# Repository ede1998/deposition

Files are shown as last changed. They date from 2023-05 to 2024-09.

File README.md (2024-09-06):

# Deposition

This repository contains **Deposition** (short for *Desk Position*), a small embedded application that controls the position of an height-adjustable desk.
This is the application in action:

<video src="https://github.com/user-attachments/assets/10c666cf-5465-435d-b400-dcfeb9302840"></video>

[Video of height-adjustable desk moving up and down](./resources/demo.mp4)

## How it works

The micro controller gets inputs via 4 buttons: up, down, position 1, position 2. When one of the buttons is pressed, the desk starts moving.
Required hardware:

- 1x precision potentiometer *Bourns 3590*, supports 10 full rotations
- 1x retractable lanyard/key chain
- 1x OLED 128x64 dot matrix *SSD1306*
- 2x photo coupler *EL817*
- 4x button
- resistors
- cables
- enclosures, 3D printed
- micro controller dev board *ESP32-WROOM-32*

### Position Detection

<video src="https://github.com/user-attachments/assets/6ebd7623-417b-41c7-af76-c692e692968f"></video>

[Video of thread begin pulled, hooked onto screws and released, display shows current distance](./resources/test-bench.mp4)

The current height is detected with the micro controller's builtin ADC which is connected to a potentiometer. This potentiometer is in turn mechanically connected
to the insides of a retractable lanyard with a few 3D printed connectors. The thread of the lanyard is connected to a horizontal stabilizer bar underneath the desk.
When the height increases, the thread is pulled further out and when it is reduced, the spiral torsion (=clock) spring of the lanyard retracts the thread. This in
turn rotates the potentiometer clockwise or counterclockwise. This is how it looks inside:

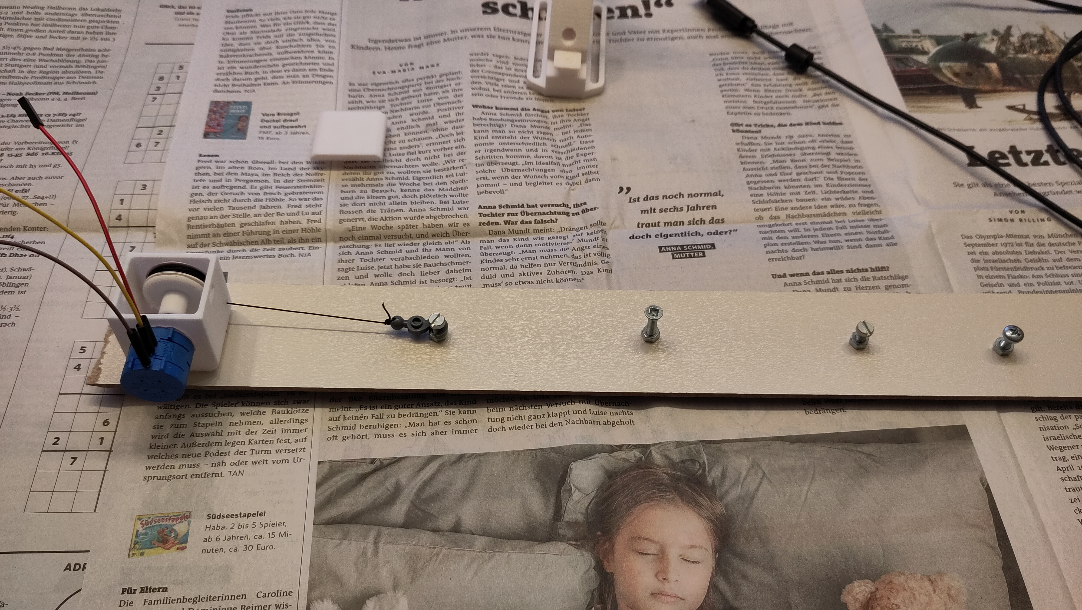
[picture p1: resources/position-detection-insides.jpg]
Insides of a retractable lanyard connected to a potentiometer with a 3D printed part, everything mounted on a long wooden board with screws in regular intervals, a thread is connecting the retractable lanyard to one of the screws


Further details can be found in [resources/height-adjustable-desk.pdf](resources/height-adjustable-desk.pdf).

### Control of the desk motors

The desk is moved by motors located in the desk's legs. The were pre-installed in the commercial product and could be controlled with two buttons: up and down.
However, the control panel did not support moving to a memorized position. For **Deposition**, the buttons were replaced with photo couplers to emulate their
open/closed behavior while keeping the two circuits electrically separated.

The circuit diagram can be found in [resources/height-adjustable-desk.pdf](resources/height-adjustable-desk.pdf).

### Enclosure

The enclosures were designed in FreeCAD and later on in OpenSCAD. They are all 3D printed. All models can be found under <./cad>.

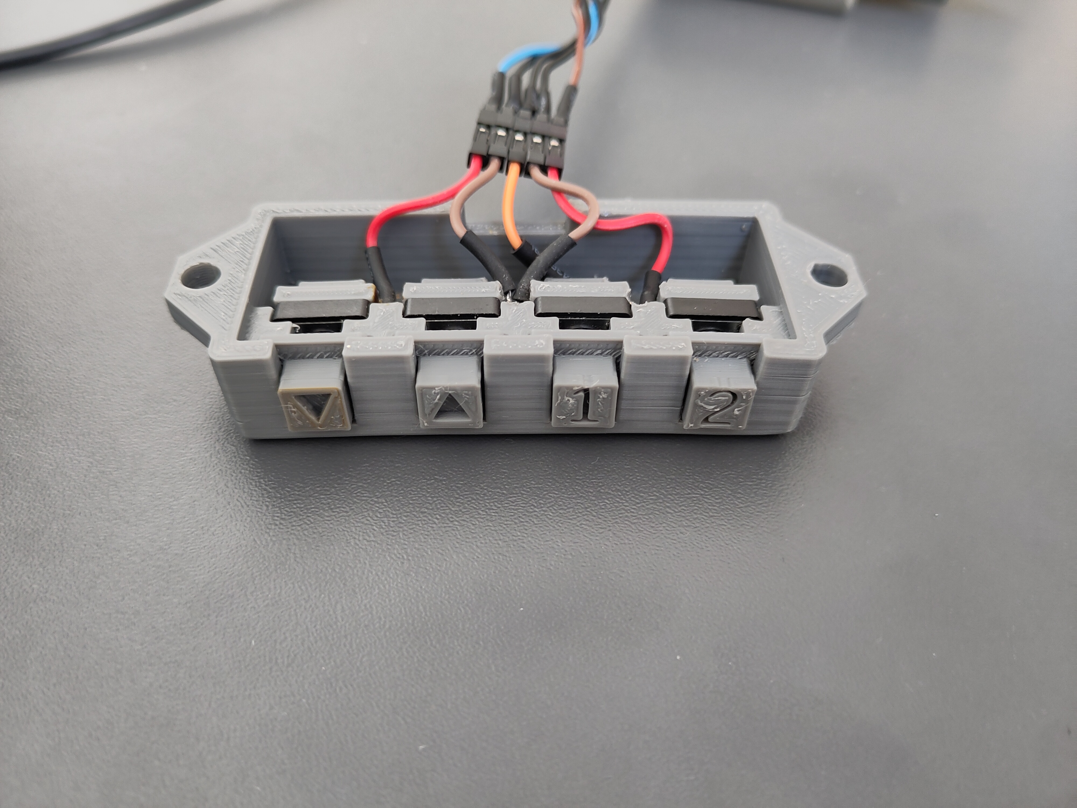
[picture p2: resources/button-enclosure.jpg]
Cuboid enclosure with four button protruding out the front and some cables going out the back


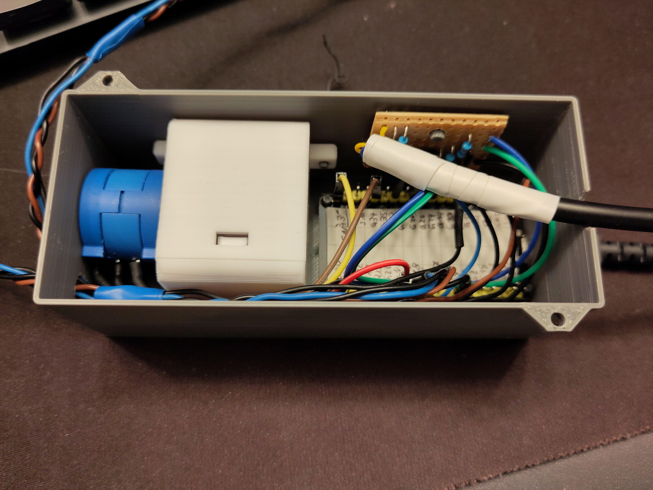
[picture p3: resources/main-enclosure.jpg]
Cuboid enclosure containing ESP32 dev board, potentiometer, a small PCB and lots of cables


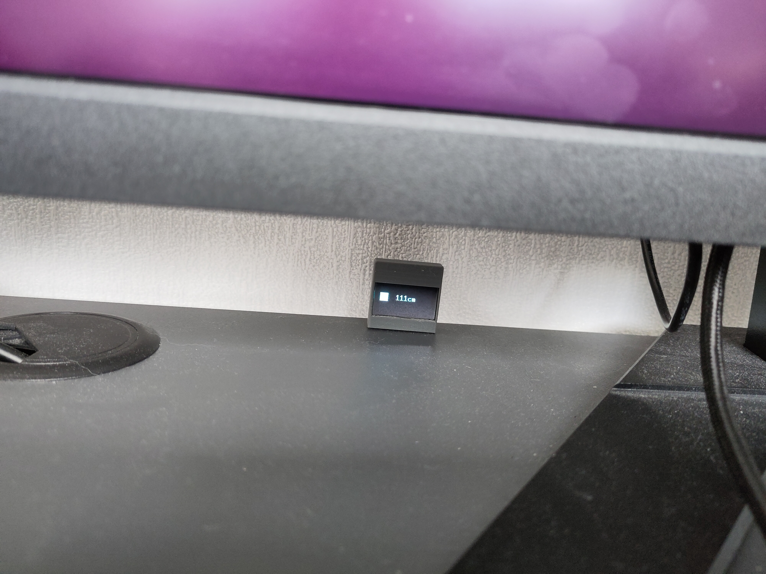
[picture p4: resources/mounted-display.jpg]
Small display inside 3D printed enclosure mounted on rear edge of desk


## Lessons learned

- General 3D design with FreeCAD and OpenSCAD was not hard after getting used to the general design process.
- Rust embedded ecosystem is nice: GPIO pins cannot be used multiple times by accident because you take ownership.
- Twisting wires is a bad idea if they are not a differential pair. I could not even get buttons or display (with 10Hz I2C) to work this way.

## Development environment

In addition to normal Rust, [install the ESP32 Rust toolchain](https://docs.esp-rs.org/book/installation/riscv-and-xtensa.html) via `espup`.
Remember to always `source ~/export-esp.sh`. You can then use the normal `cargo` commands, e.g. `cargo run --release`[^1] to compile and flash
the program onto the micro controller if it is connected.

[^1]: Debug mode will likely not working due to timing-sensitive peripherals.

For testing, [Wokwi](https://github.com/wokwi/wokwi-cli) is available. Unfortunately, the committed test does not work because it fails to read from
the persistent memory. The test can be run with `wokwi-cli --scenario wokwi-tests/go_to_options.test.yaml` if Wokwi is installed in v0.14.0 (and possibly others).
Wokwi also requires the environment variables `WOKWI_CLI_TOKEN` and `GITHUB_TOKEN` to be set.

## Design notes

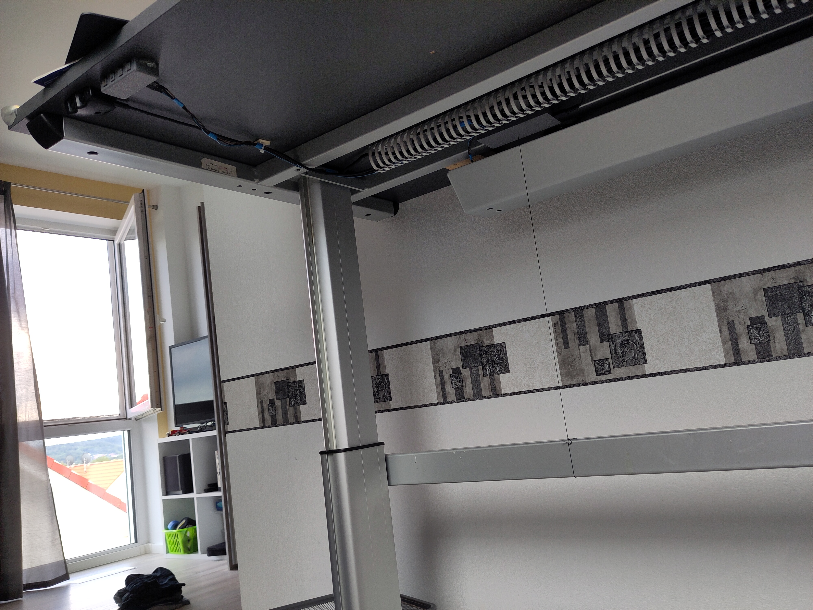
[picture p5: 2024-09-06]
resources/thread-underneath-desk.jpg

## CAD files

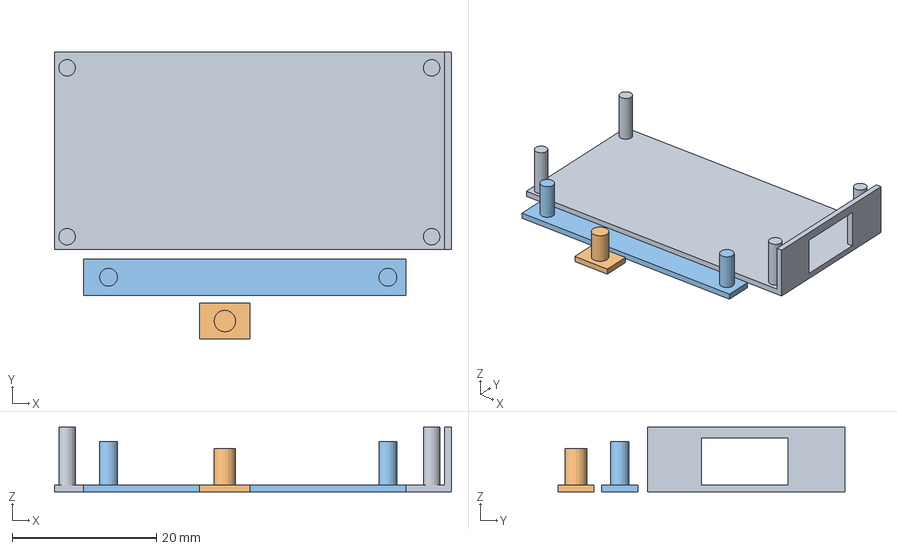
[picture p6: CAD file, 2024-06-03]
cad/SS_main-housing_test.3mf
55.0 x 39.8 x 9.00 mm
main-housing_esp_test.stl(2)
main-housing_opto_test.stl
main-housing_spool_test.stl

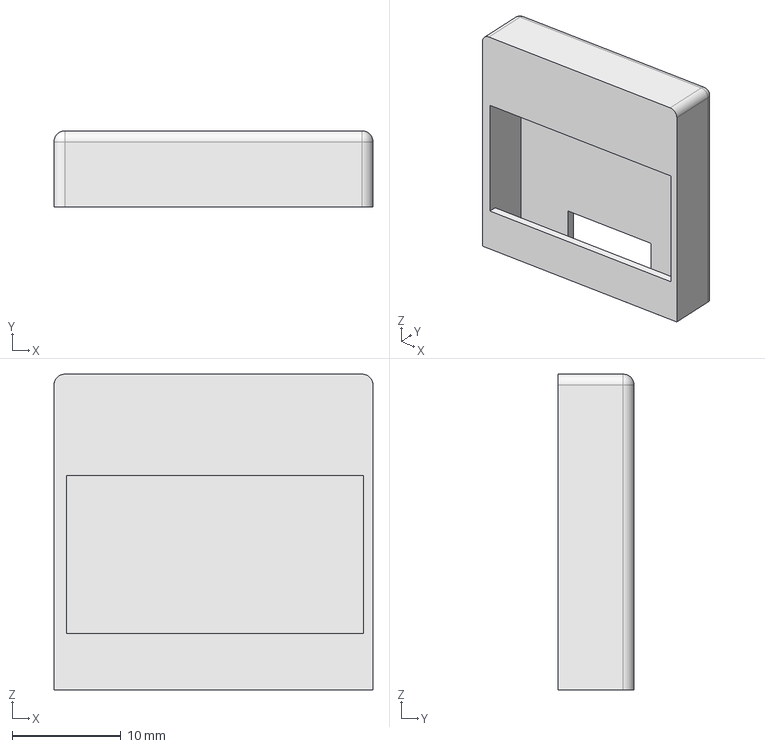
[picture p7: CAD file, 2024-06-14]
cad/display-housing.FCStd
29.3 x 7.00 x 29.0 mm

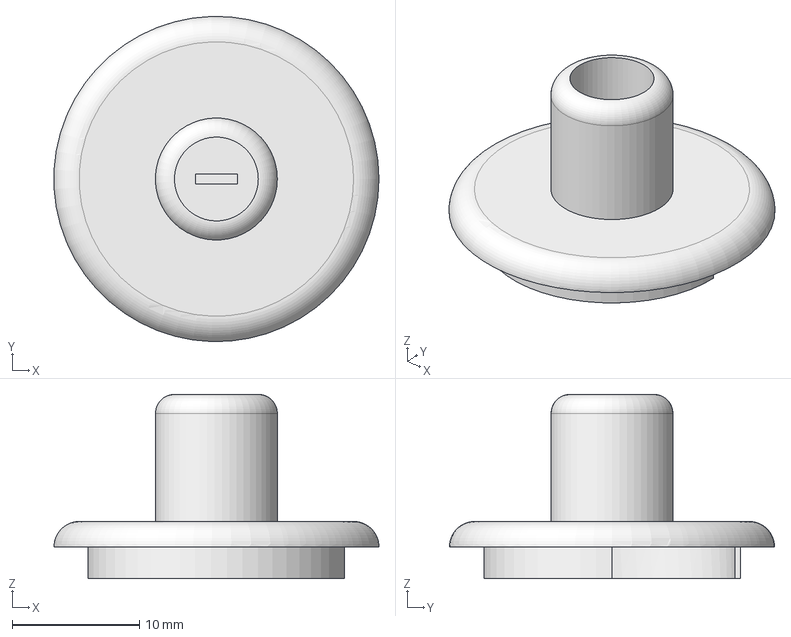
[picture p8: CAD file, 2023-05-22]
cad/poti-connector.FCStd
25.6 x 25.6 x 14.5 mm

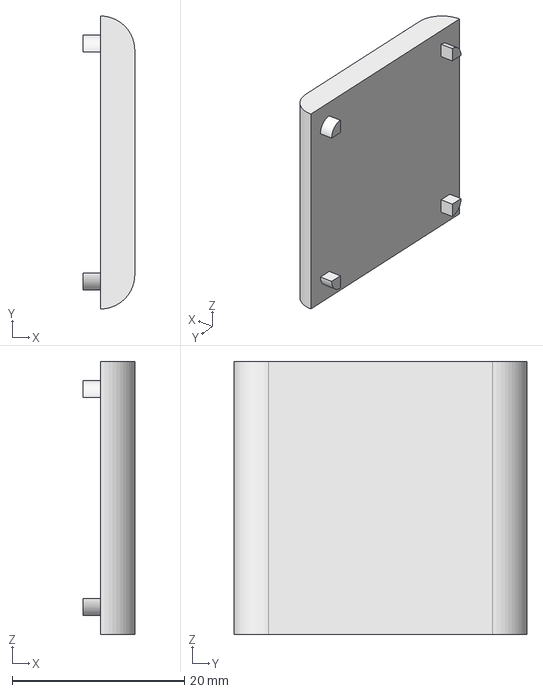
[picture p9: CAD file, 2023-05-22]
cad/minimal-case.FCStd
6.00 x 34.0 x 31.7 mm

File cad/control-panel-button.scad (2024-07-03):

include <BOSL/constants.scad>
use <BOSL/transforms.scad>
use <BOSL/shapes.scad>

$fn = 20;

touch_area = [7.5, 7.5, 5];
engraving_depth = 1.6;
retainer = [13,13,1.5];
engraving =
    //"1";
    //"2";
    //"▲";
    "▼";

upcube(retainer);
up(retainer.z) {
    difference() {
        upcube(touch_area);
        up(touch_area.z) mirror([0,0,1]) linear_extrude(engraving_depth) text(engraving, size = 6.5, valign = "center", halign = "center");
    }
}

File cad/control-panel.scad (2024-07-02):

include <BOSL/constants.scad>
use <BOSL/masks.scad>
use <BOSL/shapes.scad>

$fn = 20;

container_inner = [65, 25, 12.3];
container_thickness = 3;

connector_gap_height = 3.5;
connector_gap_width = 13.7;

button_height = 11.9;
button_length = 11.9;
button_base_width = 3.7;
button_prongs_distance = 12.5;
button_prongs_length = 2.8;
button_clicker_bump = 3.3;
button_clicker_clearance = 0.3;

button_face = 8;

module brace(lengths, height, thicknesses) {
    assert(len(lengths) == 2, "Requires 2 length values, one for each leg");
    assert(len(thicknesses) == 2, "Requires 2 thickness values, one for each leg");
    linear_extrude(height = height)
        polygon(points = [[0,0], [0, thicknesses.y], [lengths.x, thicknesses.y], [lengths.x, thicknesses.y + lengths.y], [lengths.x + thicknesses.x, thicknesses.y + lengths.y], [lengths.x + thicknesses.x,0]]);
}


module button_brace() {
    brace_thickness = 3;
    button_center_x = button_length / 2 + brace_thickness;
    cover_brace_thickness = [2,2];
    cover_brace_lengths = [3,2.4];
    cover_length = button_length +2;
    cover_brace_start_y = - (button_clicker_bump - brace_thickness);
    
    translate([-button_center_x, cover_brace_lengths.y  - brace_thickness + (button_clicker_bump - button_clicker_clearance), 0]) {
        translate([button_center_x - 0.5 * button_prongs_distance, button_base_width + brace_thickness,0]) cube([button_prongs_distance, button_prongs_length, button_height]);
        extra_support = [button_prongs_distance * 0.7, 4, button_height * 0.8];
        translate([button_center_x - 0.5 * extra_support.x, button_base_width + brace_thickness + button_prongs_length, 0]) cube(extra_support);
        
        translate([2*brace_thickness,0,0]) mirror([1,0,0]) brace([brace_thickness, brace_thickness], button_height, [brace_thickness, brace_thickness - 0.2]);
        translate([button_length,0,0]) brace([brace_thickness, brace_thickness], button_height, [brace_thickness, brace_thickness - 0.2]);
    }
    
    translate([-button_center_x, cover_brace_lengths.y + cover_brace_thickness.y - cover_brace_start_y, 0]) {
        distance_from_center = 0.5 * cover_length - cover_brace_lengths[0];
        translate([button_center_x + distance_from_center, cover_brace_start_y,0]) mirror([0,1,0]) brace(cover_brace_lengths, button_height, cover_brace_thickness);
        translate([button_center_x - distance_from_center, cover_brace_start_y,0]) rotate([0,0,180]) brace(cover_brace_lengths, button_height, cover_brace_thickness);
    }
}

module screw_fixture(diameter, thickness) {
    side = diameter * 1.5;
    translate([-2*side, -side, 0]) difference() {
        cube([side, side, thickness]);
        translate([side/2,side/2, -thickness*0.05]) cylinder(h = thickness * 1.1, d = diameter);
    }
    translate([-side,0,0]) rotate([90,0,0]) right_triangle([side, thickness, side]);
    translate([-2*side,0,0]) rotate([90,0,-90]) right_triangle([side, thickness, side]);
}

module main() {
    translate([0,0, 0.5 * container_inner.z]) difference() {
        cuboid([container_inner.x + container_thickness * 2, container_inner.y + container_thickness * 2, container_inner.z + container_thickness], fillet=2, edges = EDGES_ALL - EDGES_TOP);
        cube(container_inner, center = true);
        translate([0,0, 0.8*container_inner.z]) cube(container_inner, center = true); // Remove roof
        for (i = [-1.5:1.5]) {
            translate([i * (button_length + 4), -0.5*container_inner.y, (button_length + 5)/2-0.5*container_inner.z]) cube([button_face,container_thickness*2.5, button_face+5], center = true);
        }
        translate([0, container_inner.y / 2 - 0.5 * container_thickness, container_inner.z / 2 + container_thickness - connector_gap_height + 0.25])
            backcube([connector_gap_width, container_thickness * 2, connector_gap_height]);
    }
    
    button_start_y = -container_inner[1] /2;
    for (i = [-1.5:1.5]) {
        translate([i * (button_length + 4), button_start_y, 0]) button_brace();
    }
    
    diameter = 5;
    thickness = 4;
    screw_fixture_position_xy = [container_inner.x / 2 + container_thickness, 4.5 * 0.5 * diameter];
    screw_fixture_position_z = container_inner.z - thickness + container_thickness / 2;
    translate(concat(screw_fixture_position_xy, screw_fixture_position_z))
        rotate([0,0,90])
            screw_fixture(diameter = diameter, thickness = thickness);
    translate(concat(-1 *screw_fixture_position_xy, screw_fixture_position_z))
        rotate([0,0,270])
            screw_fixture(diameter = diameter, thickness = thickness);
}

intersection() {
    main();
//    translate([5.5,-7,-2]) cube([button_length+8,24,button_height+container_thickness + 30], center = true);
//    #translate([3.5,width/2+3,-5.5]) rotate([0,0,180]) cube([spool_fixture_distance + 6, wall_thickness * 5, 5]); // spool
//    #translate([23.5,width/2-15,8.5]) cube([7, wall_thickness * 10, 5]); // optocoupler
}

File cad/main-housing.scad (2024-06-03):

include <BOSL/constants.scad>
use <BOSL/masks.scad>
use <BOSL/shapes.scad>

$fn = 20;
wall_thickness = 2;
length = 110;
width = 45;
height = 40;

esp_mount_hole_diameter = 2.3;
esp_mount_hole_distance_long = 50.7;
esp_mount_hole_distance_short = 23.4;
esp_mount_hole_distance_front = 1.5;

spool_fixture_distance = 38.7;
spool_fixture_diameter = 2.2;
yarn_hole_radius = 1;
yarn_hole_distance_from_bottom = 10;
yarn_hole_distance_from_closer_fixture = 8.4;

usb_hole_width = 9.3;
usb_hole_height = 4;

module spool() {
    rotate([-90,0,-90]) {
        import("minimal-case-body_lid.stl");
        import("minimal-case-body_body.stl");
        translate([0,0,-19.8]) cylinder(h = 19.8, d = 22.3);
    }
}
module esp() {
    cube([54.6, 28.3, 13.0], center = true);
}

module optocouplers() {
    cube([31, 8, 24], center = true);
}

%translate([27,0,-10]) union() {
    esp();
    translate([-61,0,7]) spool();
    translate([0, width/2 - 4, 15]) optocouplers();
}

module spool_fixtures(height) {
    rotate([90, 0, 0]) union() {
        cylinder(h = height, d = spool_fixture_diameter);
        translate([-spool_fixture_distance, 0, 0]) cylinder(h = height, d = spool_fixture_diameter);
    }
}

module yarn_hole() {
    hull_bottom = -(height + wall_thickness) / 2;
    pos_short = width/2 - yarn_hole_distance_from_bottom;
    pos_long = -yarn_hole_distance_from_closer_fixture+spool_fixture_diameter/2;
    translate([pos_long, pos_short, hull_bottom - wall_thickness * 0.5])
        cylinder(h = wall_thickness * 1.5, r = yarn_hole_radius);
}

module usb_hole() {
    translate([length/2,0,-(height-usb_hole_height)/2])
        cube([wall_thickness*1.5, usb_hole_width, usb_hole_height], center = true);
}

module esp_mount_fixtures(fixture_height) {
    translate([wall_thickness + esp_mount_hole_distance_front - esp_mount_hole_diameter/2 + 0.2, -esp_mount_hole_distance_short / 2, -height/2])
        union() {
            cylinder(h = fixture_height, d = esp_mount_hole_diameter);
            translate([esp_mount_hole_distance_long,0,0]) cylinder(h = fixture_height, d = esp_mount_hole_diameter);
            translate([0,esp_mount_hole_distance_short,0]) cylinder(h = fixture_height, d = esp_mount_hole_diameter);
            translate([esp_mount_hole_distance_long,esp_mount_hole_distance_short,0]) cylinder(h = fixture_height, d = esp_mount_hole_diameter);
        }
}

module optocouplers_fixture(fixture_height) {
    rotate([90,0,0]) cylinder(h = fixture_height, d = 3.3);
}

module cables_hole(diameter) {
    rotate([0,90,0]) translate([0,0,-wall_thickness]) cylinder(h = wall_thickness * 1.5, d = diameter);
}

module screw_fixture(diameter, thickness) {
    side = diameter * 1.5;
    translate([-2*side, -side, 0]) difference() {
        cube([side, side, thickness]);
        translate([side/2,side/2, -thickness*0.05]) cylinder(h = thickness * 1.1, d = diameter);
    }
    translate([-side,0,0]) rotate([90,0,0]) right_triangle([side, thickness, side]);
    translate([-2*side,0,0]) rotate([90,0,-90]) right_triangle([side, thickness, side]);
}

module main() {
    // basic hull
    let (
        container_inner = [length, width, height],
        container_outer = [ for (i = container_inner) i + wall_thickness ]
    ) {
        difference() {
            fillet(fillet=1.5, size=container_outer, edges=EDGES_Z_ALL, $fn=24) {
                cube(container_outer, center = true); // outer wall
            }
            cube(container_inner, center = true); // inner empty space
            translate([0, 0, height / 2]) cube([length, width, height], center = true); // remove top
            yarn_hole();
            usb_hole();
            translate([-length/2,-0.7 * width/2,0]) cables_hole(diameter = 5);
        }
    }
    
    translate([1, width/2, -3]) spool_fixtures(height = 6);
    esp_mount_fixtures(fixture_height = 8);
    translate([27, width/2, 11]) optocouplers_fixture(fixture_height = 5);
    
    screw_fixture_position_xy = [length / 2 - wall_thickness, - 0.5 * (width + wall_thickness)];
    screw_fixture_position_z = height / 2 - 2;
    translate(concat(screw_fixture_position_xy, screw_fixture_position_z)) screw_fixture(diameter = 3, thickness = 3);
    translate(concat(-1 *screw_fixture_position_xy, screw_fixture_position_z))
        rotate([0,0,180])
            screw_fixture(diameter = 3, thickness = 3);
}

intersection() {
    main();
//    #translate([1,-width/2+9,-height/2-wall_thickness]) cube([esp_mount_hole_distance_long + 6,esp_mount_hole_distance_short + 4,wall_thickness * 5]); // esp
//    #translate([3.5,width/2+3,-5.5]) rotate([0,0,180]) cube([spool_fixture_distance + 6, wall_thickness * 5, 5]); // spool
//    #translate([23.5,width/2-15,8.5]) cube([7, wall_thickness * 10, 5]); // optocoupler
}

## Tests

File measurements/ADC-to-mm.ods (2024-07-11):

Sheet: Sheet1
ADC | mm
952 | 86
1432 | 172
1893 | 258
2204 | 316
2572 | 386
 | 952 | 86
 | 2572 | 386
slope | 0,185185185185185 | 94,8148148148148
offset | -90,2962962962963 | -46231,7037037037
1000 | 94,8888888888889
1200 | 131,925925925926
1400 | 168,962962962963
1600 | 206
1800 | 243,037037037037
2000 | 280,074074074074
2200 | 317,111111111111
2400 | 354,148148148148
2600 | 391,185185185185

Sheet: Sheet2
No-capa | With-capa
2570 | 2598
2543 | 2603
2572 | 2603
2543 | 2600
2571 | 2609
2568 | 2601
2569 | 2604
2575 | 2599
2560 | 2602
2575 | 2607
2580 | 2605
2575 | 2602
2560 | 2601
2550 | 2604
2574 | 2595
2548 | 2607
2580 | 2590
2572 | 2606
2564 | 2597
2573 | 2597
2570 | 2598
2546 | 2604
2576 | 2607
2575 | 2598
2575 | 2607
2562 | 2603
2569 | 2600
2569 | 2607
2573 | 2604
2544 | 2602
2563 | 2605
2561 | 2607
2560 | 2595
2542 | 2605
2585 | 2607
2560 | 2613
2570 | 2598
2574 | 2607
2579 | 2589
2550 | 2603
2575 | 2607
2570 | 2605
2572 | 2602
2565 | 2600
2561 | 2598
2571 | 2590
2560 | 2596
2569 | 2604
2573 | 2604
2543 | 2605
2561 | 2606
2560 | 2600
2578 | 2609
2575 | 2596
2569 | 2606
2561 | 2605
2572 | 2598
2550 | 2609
2573 | 2598
2565 | 2607
2575 | 2594
2575 | 2605
2569 | 2607
2560 | 2606
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

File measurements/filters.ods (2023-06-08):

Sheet: mov_avg_3
2577 | 2569
2506 | 2541
2589 | 2557
2589 | 2561
2495 | 2557
2565 | 2549
2447 | 2502
2576 | 2529
2591 | 2538
2607 | 2591
2604 | 2600
2494 | 2568
2600 | 2566
2589 | 2561
2594 | 2594
2602 | 2595
2548 | 2581
2596 | 2582
2507 | 2550
2590 | 2564
2524 | 2540
2524 | 2546
2576 | 2541
2573 | 2557
2584 | 2577
2587 | 2581
2584 | 2585
2576 | 2582
2586 | 2582
2565 | 2575
2585 | 2578
2606 | 2585
2607 | 2599
2501 | 2571
2450 | 2519
2607 | 2519
2462 | 2506
2584 | 2551
2602 | 2549
2593 | 2593
2469 | 2554
2561 | 2541
2526 | 2518
2448 | 2511
2582 | 2518
2575 | 2535
2584 | 2580
2586 | 2581
2590 | 2586
2582 | 2586
2581 | 2584
2580 | 2581
2592 | 2584
2460 | 2544
2498 | 2516
2584 | 2514
2589 | 2557
2477 | 2550
2475 | 2513
2467 | 2473
2584 | 2508
2587 | 2546
2581 | 2584
2473 | 2547
2579 | 2544
2575 | 2542
2575 | 2576
2584 | 2578
2459 | 2539
2515 | 2519
2488 | 2487
2575 | 2526
2589 | 2550
2456 | 2540
2607 | 2550
2444 | 2502
2478 | 2509
2496 | 2472
2588 | 2520
2592 | 2558
2590 | 2590
2506 | 2562
2544 | 2546
2481 | 2510
2497 | 2507
2574 | 2517
2517 | 2529
2591 | 2560
2457 | 2521
2490 | 2512
2606 | 2517
2592 | 2562
2591 | 2596
2560 | 2581
2575 | 2575
2495 | 2543
2604 | 2558
2589 | 2562
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

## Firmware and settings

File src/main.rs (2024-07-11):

#![no_std]
#![no_main]
#![feature(type_alias_impl_trait)]

use debouncr::DebouncerStateful;
use embassy_time::{Duration, Instant, Ticker, Timer};
use embedded_graphics::{draw_target::DrawTarget, pixelcolor::BinaryColor};
use esp_backtrace as _;
use esp_println::logger::init_logger;
use hal::{
    analog::adc::{Adc, AdcConfig, AdcPin, Attenuation},
    clock::ClockControl,
    gpio::{Gpio34, Io, Level, Pull},
    i2c::I2C,
    peripherals::{Peripherals, ADC1},
    prelude::*,
    system::SystemControl,
    timer::timg::TimerGroup,
};
use heapless::String;
use ssd1306::{prelude::*, I2CDisplayInterface, Ssd1306};

mod data;
mod gui;
mod input;
mod operation_mode;
mod storage;
mod string_format;

use crate::{
    data::{Direction, CALIBRATION, DIRECTION, GUI_MENU, HEIGHT, INPUT, RAW_HEIGHT},
    input::{Inputs, State},
    storage::CONFIGURATION,
};

async fn poll<T, E>(mut f: impl FnMut() -> nb::Result<T, E>) -> Result<T, E> {
    loop {
        match f() {
            Ok(ok) => break Ok(ok),
            Err(nb::Error::Other(err)) => break Err(err),
            Err(nb::Error::WouldBlock) => {} // todo: do we want to keep a busy loop here? the measure task starved with this: `embassy_futures::yield_now().await,`
        }
    }
}

fn compute_median(samples: &mut [u16]) -> u16 {
    samples.sort_unstable();
    let len = samples.len();
    if len % 2 == 0 {
        let right_mid = samples[len / 2];
        let left_mid = samples[(len / 2) - 1];
        (right_mid + left_mid) / 2
    } else {
        samples[len / 2]
    }
}

const SAMPLE_COUNT: usize = if cfg!(debug_assertions) { 32 } else { 64 };

type InputPin = hal::gpio::AnyInput<'static>;
type OutputPin = hal::gpio::AnyOutput<'static>;

#[embassy_executor::task]
async fn drive(mut up: OutputPin, mut down: OutputPin) {
    up.set_low();
    down.set_low();
    loop {
        Timer::after(Duration::from_millis(5)).await;
        let Some(direction) = DIRECTION.planned().await else {
            continue;
        };
        log::info!("starting to drive in direction {direction}");
        match direction {
            Direction::Up => {
                down.set_low();
                up.set_high();
            }
            Direction::Down => {
                up.set_low();
                down.set_high();
            }
            Direction::Stopped => {
                up.set_low();
                down.set_low();
            }
            Direction::ResetDrive => {
                up.set_high();
                down.set_high();
            }
        }
        DIRECTION.acknowledge(direction).await;
    }
}

#[embassy_executor::task]
async fn read_input(up: InputPin, down: InputPin, pos1: InputPin, pos2: InputPin) {
    struct DebouncedPin {
        pin: InputPin,
        debouncer: DebouncerStateful<u8, debouncr::Repeat2>,
    }

    impl DebouncedPin {
        fn new(pin: InputPin) -> Self {
            let debouncer = debouncr::debounce_stateful_2(false);
            Self { pin, debouncer }
        }

        fn update_input(&mut self, input: &mut State) {
            let active = self.pin.is_low();
            let Some(state) = self.debouncer.update(active) else {
                return;
            };
            match state {
                debouncr::Edge::Rising => input.press(),
                debouncr::Edge::Falling => input.release(),
            }
        }
    }

    let mut up = DebouncedPin::new(up);
    let mut down = DebouncedPin::new(down);
    let mut pos1 = DebouncedPin::new(pos1);
    let mut pos2 = DebouncedPin::new(pos2);

    let mut inputs = Inputs::default();

    loop {
        up.update_input(&mut inputs.up);
        down.update_input(&mut inputs.down);
        pos1.update_input(&mut inputs.pos1);
        pos2.update_input(&mut inputs.pos2);

        *INPUT.lock().await = inputs.clone();

        Timer::after(Duration::from_millis(5)).await;
    }
}

#[embassy_executor::task]
async fn measure_task(gpio34: Gpio34, adc: ADC1) {
    measure(gpio34, adc).await.expect("measure task failed");
}

async fn measure(pin: Gpio34, adc: ADC1) -> Result<(), &'static str> {
    let mut adc1_config = AdcConfig::new();
    let mut pin34 = adc1_config.enable_pin(pin, Attenuation::Attenuation11dB);
    let mut adc1 = Adc::<ADC1>::new(adc, adc1_config);

    let mut calibration = CONFIGURATION.lock().await.get().calibration.clone();

    let mut last_log = Instant::now();
    loop {
        if CALIBRATION.signaled() {
            calibration = CALIBRATION.wait().await;
        }

        let pin25_value = read_sample(&mut adc1, &mut pin34).await?;

        let value = calibration.transform(pin25_value);

        if log::log_enabled!(log::Level::Trace) && last_log.elapsed() > Duration::from_millis(250) {
            log::trace!("new height {} (={pin25_value}) measured", value.as_mm());
            last_log = Instant::now();
        }
        *HEIGHT.lock().await = value;
        RAW_HEIGHT.signal(pin25_value);
        Ticker::every(Duration::from_millis(5)).next().await;
    }
}

async fn read_sample<'a>(
    adc1: &mut Adc<'a, ADC1>,
    pin34: &mut AdcPin<Gpio34, ADC1>,
) -> Result<u16, &'static str> {
    let mut samples = heapless::Vec::<_, SAMPLE_COUNT>::new();
    for _ in 0..samples.capacity() {
        let sample = poll(|| adc1.read_oneshot(pin34))
            .await
            .map_err(|_| "failed to read ADC value")?;

        samples.push(sample).map_err(|_| "failed to store sample")?;
    }

    Ok(compute_median(&mut samples))
}

#[embassy_executor::task]
async fn display_task(i2c: I2C<'static, hal::peripherals::I2C0, hal::Blocking>) {
    display(i2c).await.expect("display task failed");
}

fn str_to_owned<const N: usize>(text: &str) -> String<N> {
    text.try_into()
        .expect("Length of str exceeds String capacity")
}

async fn display(
    i2c: I2C<'static, hal::peripherals::I2C0, hal::Blocking>,
) -> Result<(), String<150>> {
    let interface = I2CDisplayInterface::new(i2c);
    let mut display = Ssd1306::new(interface, DisplaySize128x64, DisplayRotation::Rotate180)
        .into_buffered_graphics_mode();
    display
        .init()
        .map_err(|e| format!(150, "display initialization failed: {e:?}"))?;

    loop {
        let menu = GUI_MENU.wait().await;

        display
            .clear(BinaryColor::Off)
            .map_err(|e| format!(150, "clearing display failed: {e:?}"))?;
        menu.display(&mut display).await.map_err(str_to_owned)?;
        display
            .flush()
            .map_err(|e| format!(150, "flushing failed: {e:?}"))?;
    }
}

#[embassy_executor::task]
async fn run() {
    operation_mode::run().await.expect("run task failed");
}

#[main]
async fn main(spawner: embassy_executor::Spawner) {
    init_logger(log::LevelFilter::Trace);
    log::info!("init!");
    let peripherals = Peripherals::take();
    let system = SystemControl::new(peripherals.SYSTEM);
    let clocks = ClockControl::boot_defaults(system.clock_control).freeze();

    let timer_group0 = TimerGroup::new_async(peripherals.TIMG0, &clocks);
    esp_hal_embassy::init(&clocks, timer_group0);

    let io = Io::new(peripherals.GPIO, peripherals.IO_MUX);
    let adc = peripherals.ADC1;
    // Create a new peripheral object with the described wiring
    // and standard I2C clock speed
    let i2c = I2C::new(
        peripherals.I2C0,
        io.pins.gpio32,
        io.pins.gpio27,
        100u32.kHz(),
        &clocks,
        None,
    );
    let btn_up = InputPin::new(io.pins.gpio18, Pull::Up);
    let btn_down = InputPin::new(io.pins.gpio19, Pull::Up);
    let btn_pos1 = InputPin::new(io.pins.gpio4, Pull::Up);
    let btn_pos2 = InputPin::new(io.pins.gpio5, Pull::Up);
    let height_meter = io.pins.gpio34;

    let up = OutputPin::new(io.pins.gpio25, Level::Low);
    let down = OutputPin::new(io.pins.gpio26, Level::Low);

    spawner.spawn(measure_task(height_meter, adc)).unwrap();
    spawner.spawn(display_task(i2c)).unwrap();
    spawner
        .spawn(read_input(btn_up, btn_down, btn_pos1, btn_pos2))
        .unwrap();
    spawner.spawn(drive(up, down)).unwrap();
    spawner.spawn(run()).unwrap();
}

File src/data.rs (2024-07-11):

use core::cmp::Ordering;

use embassy_sync::blocking_mutex::raw::CriticalSectionRawMutex;
use heapless::Vec;
use serde::{Deserialize, Serialize};

use crate::{gui::MainMenu, input::Inputs};

pub type Mutex<T> = embassy_sync::mutex::Mutex<CriticalSectionRawMutex, T>;
pub type Signal<T> = embassy_sync::signal::Signal<CriticalSectionRawMutex, T>;

pub static HEIGHT: Mutex<Millimeters> = Mutex::new(Millimeters(0));
pub static RAW_HEIGHT: Signal<u16> = Signal::new();
pub static INPUT: Mutex<Inputs> = Mutex::new(Inputs::new());

pub static GUI_MENU: Signal<MainMenu> = Signal::new();

pub static DIRECTION: DirectionControl = DirectionControl::new();

pub struct DirectionControl {
    requested: Mutex<Direction>,
    current: Mutex<Direction>,
}

impl DirectionControl {
    pub const fn new() -> Self {
        Self {
            requested: Mutex::new(Direction::Stopped),
            current: Mutex::new(Direction::Stopped),
        }
    }

    pub async fn request(&self, new_direction: Direction) {
        log::debug!("driving in direction {new_direction} requested.");
        *self.requested.lock().await = new_direction;
    }

    pub async fn planned(&self) -> Option<Direction> {
        let (cur, req) = {
            let cur_guard = self.current.lock().await;
            let req_guard = self.requested.lock().await;
            (*cur_guard, *req_guard)
        };

        Some(req).filter(|&req| req != cur)
    }

    pub async fn acknowledge(&self, direction: Direction) {
        *self.current.lock().await = direction;
    }
}

pub static CALIBRATION: Signal<Calibration> = Signal::new();

type Mapping = (u16, Millimeters);

#[derive(Debug, Clone, Deserialize, Serialize)]
pub struct Calibration {
    fix_points: Vec<Mapping, 20>,
}

impl core::ops::Deref for Calibration {
    type Target = Vec<Mapping, 20>;

    fn deref(&self) -> &Self::Target {
        &self.fix_points
    }
}

impl Calibration {
    pub const fn new() -> Self {
        Self {
            fix_points: Vec::new(),
        }
    }

    pub fn insert(&mut self, adc: u16, height: Millimeters) -> Result<(), &'static str> {
        let position = self.fix_points.binary_search_by_key(&adc, |(adc, _)| *adc);
        match position {
            Ok(index) => {
                self.fix_points[index] = (adc, height);
            }
            Err(index) => {
                self.fix_points
                    .insert(index, (adc, height))
                    .map_err(|_| "too many calibration points")?;
            }
        }
        Ok(())
    }

    pub fn clear(&mut self) {
        self.fix_points.clear();
    }

    pub fn remove(&mut self, index: usize) {
        self.fix_points.remove(index);
    }
    pub fn transform(&self, reading: u16) -> Millimeters {
        if self.fix_points.len() < 2 {
            return Millimeters::from_mm(0);
        }

        match self.fix_points.binary_search_by_key(&reading, |x| x.0) {
            Ok(i) => self.fix_points[i].1,
            Err(i) => {
                let section = if i == 0 {
                    (self.fix_points.first(), self.fix_points.get(1))
                } else if i == self.fix_points.len() {
                    (
                        self.fix_points.get(self.fix_points.len() - 2),
                        self.fix_points.last(),
                    )
                } else {
                    (self.fix_points.get(i - 1), self.fix_points.get(i))
                };

                let &(left_adc, Millimeters(left_mm)) = section.0.unwrap();
                let &(right_adc, Millimeters(right_mm)) = section.1.unwrap();
                let section_height = f64::from(right_mm.abs_diff(left_mm));
                let section_length = f64::from(right_adc.abs_diff(left_adc));
                let slope = section_height / section_length;
                let distance_reading_to_left = f64::from(reading.abs_diff(left_adc));
                let mm_from_left = slope * distance_reading_to_left;
                let mm_from_left = mm_from_left as u16;
                let abs_mm = if reading < left_adc {
                    left_mm.saturating_sub(mm_from_left)
                } else {
                    left_mm.saturating_add(mm_from_left)
                };

                Millimeters(abs_mm)
            }
        }
    }
}

#[derive(Debug, Clone, Copy, Ord, PartialEq, PartialOrd, Eq, Serialize, Deserialize)]
pub struct Millimeters(u16);

impl Millimeters {
    pub const fn from_mm(value: u16) -> Self {
        Self(value)
    }

    pub const fn is_zero(self) -> bool {
        self.0 == 0
    }

    pub const fn cmp_fuzzy_eq(
        self,
        other: Self,
        allowed_delta: Millimeters,
    ) -> core::cmp::Ordering {
        let left = self.0;
        let right = other.0;
        if left.abs_diff(right) < allowed_delta.0 {
            Ordering::Equal
        } else if left < right {
            Ordering::Less
        } else {
            Ordering::Greater
        }
    }

    pub fn increase(self) -> Self {
        Self(self.0.saturating_add(1))
    }

    pub fn decrease(self) -> Self {
        Self(self.0.saturating_sub(1))
    }

    pub fn as_cm(self) -> u16 {
        self.0 / 10
    }

    pub fn as_mm(self) -> u16 {
        self.0
    }
}

#[derive(Debug, Clone, Copy, PartialEq, Eq)]
pub enum Direction {
    Up,
    Stopped,
    Down,
    ResetDrive,
}

impl core::fmt::Display for Direction {
    fn fmt(&self, f: &mut core::fmt::Formatter) -> core::fmt::Result {
        f.write_str(match self {
            Direction::Up => "+",
            Direction::Stopped => "0",
            Direction::Down => "-",
            Direction::ResetDrive => "R",
        })
    }
}

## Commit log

2023-05-17 add cad designs
    [minimal-case.FCStd, poti-connector.FCStd]
2023-05-22 update cad designs
    [minimal-case.FCStd, poti-connector.FCStd]
2023-05-22 first try at converting ADC to mm
    [ADC-to-mm.ods]
2023-05-27 working distance compute
    [ADC-to-mm.ods]
2023-05-29 stable ADC and showing direction
2023-06-08 replace katex with internet service
    -> cargo doc works again
    [main.rs]
2023-06-08 add measurement experiments
    [filters.ods]
2023-06-11 read button input
2023-06-13 implement multi button input
2023-06-21 make button enum into bitflags
    used for multiple button gestures
2023-06-22 try fixing multi button press
    [main.rs]
2023-06-22 replace println with log
    [data.rs, main.rs]
2023-06-22 improve button handling
2023-06-22 use physically usable pin
2023-06-24 prepare calibration screen
2023-06-25 start implementing calibration menu
2023-06-25 implement adding calibration point in basic manner
2023-06-26 fix a few calibration screen bugs
    [calibration.rs]
2023-06-27 implement fast scroll for calibration
2023-06-27 fix measure task starvation
    [main.rs]
2024-06-03 CAD models for box
    [SS_main-housing_test.3mf, display-housing.FCStd, main-housing.scad]
2024-06-14 finished display housing
    [display-housing.FCStd]
2024-06-14 Change ADC port to work around limited cable length
2024-07-02 control panel design
    [control-panel-button.scad, control-panel.scad]
2024-07-02 improve control panel design after test prints
    [control-panel.scad]
2024-07-02 finalize control panel
    [control-panel.scad]
2024-07-03 add button engraving and fix height
    [control-panel-button.scad]
2024-07-11 rotate display upwards and make button go in right direction
2024-07-11 Stop earlier when moving to prevent overshooting
    [data.rs]
2024-07-11 add actual values to visualization
    [ADC-to-mm.ods]
2024-09-06 Document everything
    [ADC-to-mm.ods]
